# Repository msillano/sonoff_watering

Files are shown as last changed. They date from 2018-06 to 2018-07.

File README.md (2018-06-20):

# sonoff_watering

Tired of changing the terrace irrigation timer every 2 years, I decided to design a timer: obviously IoT and based on MQTT. 

The result is this complete DIY project of an irrigation timer, better than many commercial timers, designed and manufactured according to the state of the art. 

This timer contains a STA (WIFI client), an AP (not used), a MQTT client and a MQTT server (broker), provided with programmable logic (script): in practice a mini mosquitto + node-red on-board ! 

So in this project the operating logic is all internal: an external MQTT server 24/7 is not required (in fact I think a server 24/7 is too much to water a terrace!). The timer is totally autonomous, but at the same time always compatible with external standard MQTT clients and brokers. 

A probe monitors the state of the soil (dry/soaked, with adjustable threshold) and conditions the watering. 

Monitoring and configuration of the timer are performed with MQTT clients with dashboards, both on a PC and on a smartphone. Access is local via WIFI, but can be made Internet global using a free dynamic DNS service (example noip: https://www.noip.com/). 

While using updated and quality components, this timer is very cheap: total cost less than € 15 (US$ 18)!  All this is made possible by the happy union of two phenomenal products: 
1) Sonoff basic, economic WIFI card with power supply, microprocessor EPS8266 and relay
2) esp_MQTT, a firmware for EPS8266 created by Martin-ger, which transforms the Sonoff-basic into a tank. 

For the full story, see watering-sonoff-enXX.pdf (english version) or watering-sonoff-itXX.pdf (versione italiana).

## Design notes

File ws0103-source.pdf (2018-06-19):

% Watering-sonoff ver 1.3, GNU LGPL license, (C)2018 m.sillano % telnet: script http://192.168.43.242:85/www/sonoff/ws0103.eub

% you can change the topic and the ID in next line
config @6 /msillanohome/hidro/1

on init
do
% @8 is the run counter
% test for first run: $tmp = 0 also if @8 = '' setvar $tmp = (@8 * 1)
if $tmp = 0 then
% cool start, only for first run:
% @1: cycle timer count down (min: 0 off) setvar @1 = 0
% @2: cycle duration (min)
setvar @2 = 2
% @3: time T1
setvar @3 = "01:00"
% @4: time T2
setvar @4 = "02:00"
% @5: mode (0..4)
setvar @5 = 2
% @7: day counter (for mode 1) setvar @7 = 0
endif
% hot start
% increments run counter
setvar @8 = ($tmp + 1)
% sets topics
setvar $cmt = @6 | "/command"
setvar $set = @6 | "/set"
subscribe local $cmt
subscribe local $set
% set moisure status in var $ms gpio_pinmode 14 input
setvar $ms = gpio_in(14)
% publish status/moisure.
setvar $tmp = @6 | "/status/moisure"
publish local $tmp "{\"Time\":\"" | $timestamp | "\",\"moisure\":" | $ms | "}"
retained
% relay restore status, in var $rs
% restore from retained message...
setvar $tmp = @6 | "/status/watering"
setvar $rs = json_parse("watering",retained_topic($tmp)) if not($rs = 1) then
% default is 0
setvar $rs = 0
endif
% or from cycle timer count down if @1 > 0 then
setvar $rs = 1
% restart timer 1 (1 min)
settimer 1 60000
endif
% like a call: this publish status/watering and status/moisure publish local $cmt "go"
% sets alarms
setalarm 3 @3
setalarm 4 @4

on mqttconnect
do
% subscrive from new client all commands

subscribe remote $cmt
subscribe remote $set
% re-publish status to update new client publish local $set "{\"data\":\"send\"}" publish local $cmt "send"

on topic remote $set
do
% debug echo on console
println "on Remote Set " | $this_data
% re-publish local for execution publish local $set $this_data

on topic remote $cmt
do
% debug echo on console
println "on Remote Command " | $this_data
% re-publish local for execution
publish local $cmt $this_data

on topic local $set
do
% debug echo on console
println "on Local Set " | $this_data
% decodes the 'set' data, puts it in $tmp setvar $tmp = json_parse("data",$this_data)
if $tmp = "long" then
% sets cycle duration (min)
setvar @2 = json_parse("value",$this_data) | " "
endif
if $tmp = "when1" then
% sets time T1...
setvar @3 = json_parse("value",$this_data) % and update alarm 3
setalarm 3 @3
endif
if $tmp = "when2" then
% sets time T1...
setvar @4 = json_parse("value",$this_data) % and update alarm 4
setalarm 4 @4
endif
if $tmp = "mode" then
% sets mode (0..4)
setvar @5 = json_parse("value",$this_data) endif
if $tmp = "reset" then
% does reset
system reset
endif
if $tmp = "timezone" then
% sets timezone (see https://github.com/martin-ger/esp_mqtt/issues/36 )
system "set ntp_timezone " | json_parse("value",$this_data)
endif
% implicit 'send'
% in any case, after a 'set', publish status/config
setvar $tmp = @6 | "/status/config"
publish local $tmp "{\"run\":" | @8 | ",\"long\":" | @2 | ",\"tx\":[\"" | @3 |
"\",\"" | @4 | "\"],\"mode\":" | @5 | "}" retained

on topic local $cmt
do
% debug echo on console
println "on Local Command " | $this_data

% decodes the value
if $this_data = "on" then
% sets ON
setvar $rs = 1
endif
if $this_data = "off" then
% sets 0 cycle timer count down setvar @1 = 0
% sets OFF
setvar $rs = 0
endif
if $this_data = "toggle" then % sets 0 cycle timer count down setvar @1 = 0
% inverts relay status
setvar $rs = not($rs)
endif
% cycle starts only if moisure dry ($ms=1)
if (($this_data = "cycle")*($ms = 1)) > 0 then % sets ON
setvar $rs = 1
% initialize cycle timer count down
setvar @1 = (@2 + 1)
% start timer (60 sec)
settimer 1 60000
endif
setvar $tmp = @6 | "/status/watering"
if $this_data = "send" then
% only re-send status/*
publish local $tmp retained_topic($tmp)
setvar $tmp = @6 | "/status/moisure"
publish local $tmp retained_topic($tmp) else
% implicit 'go': set output and publish
if (($rs = 1)*(@5 = 4)) > 0 then
% mode 4, ON. Like $ms
gpio_out 12 $ms
gpio_out 13 not($ms)
else
% default
gpio_out 12 $rs
gpio_out 13 not ($rs)
endif
% publish the watering status
publish local $tmp "{\"Time\":\"" | $timestamp | "\",\"watering\":" | $rs |
"}" retained
endif

% Sonoff-basic button pressed:
on gpio_interrupt 0 pullup
do
% debug echo on console
println "New state GPIO 0: " | $this_gpio
if $this_gpio = 0 then
% toggle action
publish local $cmt "toggle"
endif

% status change of moisure probe on gpio_interrupt 14 nopullup
do
% debug echo on console
println "New state GPIO 14: " | $this_gpio
% real change?

if $ms = not($this_gpio) then
setvar $ms = $this_gpio
% publish the moisure status
setvar $tmp = @6 | "/status/moisure"
publish local $tmp "{\"Time\":\"" | $timestamp | "\",\"moisure\":" | $ms |
"}" retained
if (($rs = 1)*(@5 = 4)) > 0 then
% relay ON/OFF if mode 4 and $rs=1
gpio_out 12 $ms
gpio_out 13 not($ms)
endif
endif

% timer 1 min
on timer 1
do
% debug echo on console
println "on int timer1 " | @1
if @1 > 0 then
% down cycle timer count
setvar @1 = (@1 – 1)
% restart timer
settimer 1 60000
endif
if @1 = 1 then
% end count, sets OFF
publish local $cmt "off"
endif

% time T1 alarm
on alarm 3
do
% debug echo on console
println "on intT1"
setvar @7 = not(@7*1)
if ((@5 = 1)*(@7 = 1)) > 0 then % mode 1, if @7, starts cycle publish local $cmt "cycle" endif
if @5 > 1 then
if @5 = 4 then
% mode 4, sets ON
publish local $cmt "on"
else
% mode 2, 3: starts cycle
publish local $cmt "cycle" endif
endif

%time T2 alarm
on alarm 4
do
% debug echo on console
println "on intT2"
if @5 = 4 then
% mode 4: OFF
publish local $cmt "off"
endif
if @5 = 3 then
% mode 3: starts cycle
publish local $cmt "cycle" endif

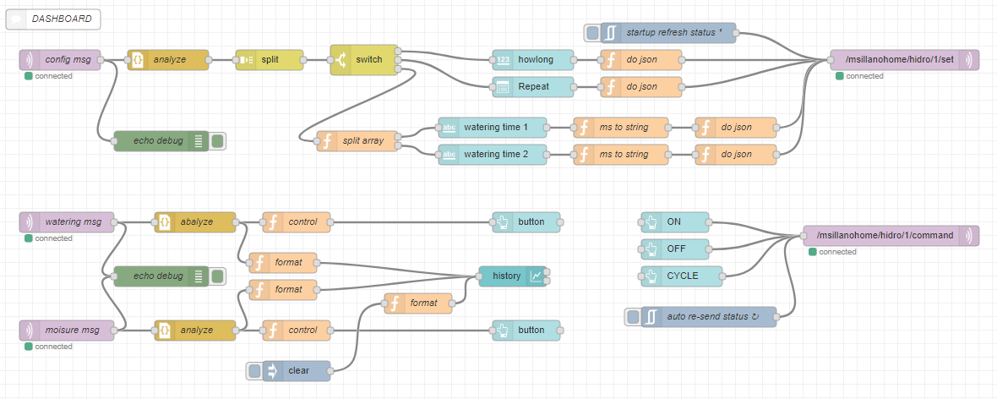
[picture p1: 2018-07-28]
images/2018-05-21.085833.shot.png

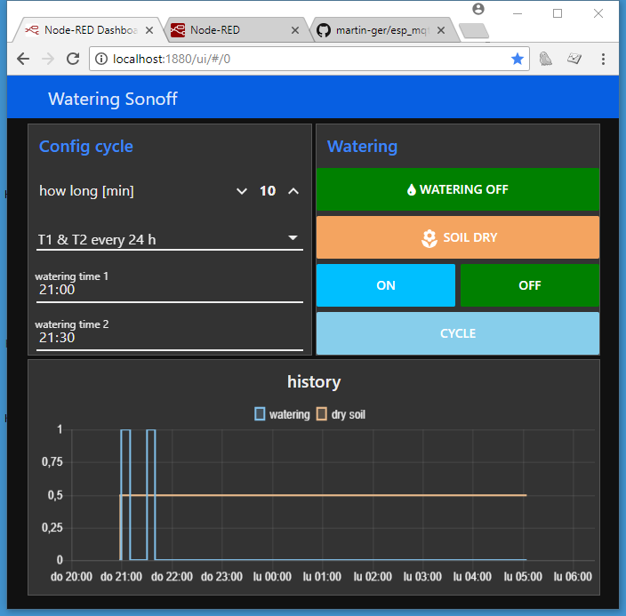
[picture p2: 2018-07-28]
images/2018-05-21.050436.shot.png

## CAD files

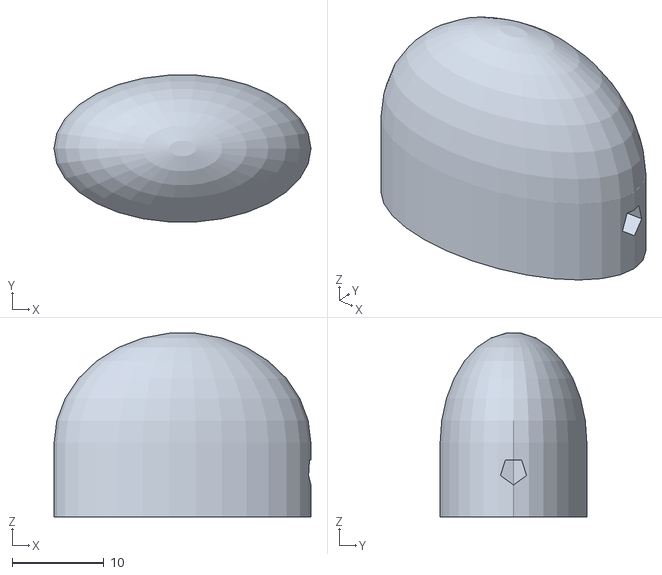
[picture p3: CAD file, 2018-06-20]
3d/sensor.stl
28.0 x 16.0 x 20.0

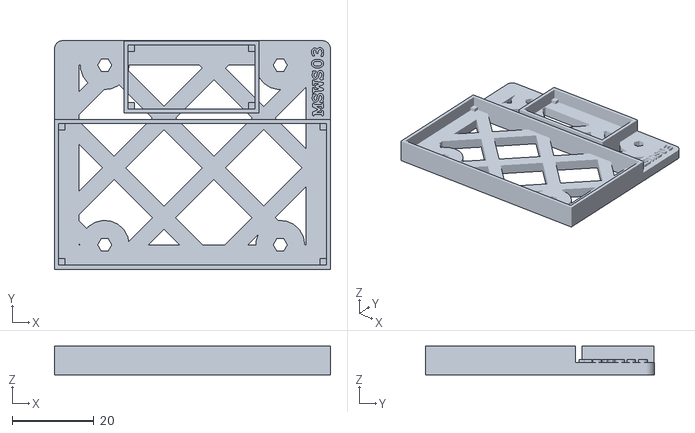
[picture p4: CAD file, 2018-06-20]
3d/e3DHW_base_lib.stl
67.6 x 56.0 x 7.00

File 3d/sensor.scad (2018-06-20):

 difference() {
   resize([28,16,20]) 
       union() {
           difference() {
                sphere(r = 12);
                sphere(r = 10);
                translate([-15, -15, -30]) {cube(size =[30,30,30]);};
           }
           translate([0, 0, -8+0.1])
                difference() {
                    cylinder(h= 8, r = 12);
                    cylinder(h= 8, r = 10);
           };
      }
      translate([10, 0, -3])rotate(a=[0,90,0])cylinder(h= 16, r = 1.5);   

    }

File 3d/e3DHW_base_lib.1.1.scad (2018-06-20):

/*
   e3DHW project © 2018 Marco Sillano  (marco.sillano@gmail.com)
   This library is free software: you can redistribute it and/or modify
   it under the terms of the GNU Lesser General Public License as published
   by the Free Software Foundation, either version 3 of the License, or
   (at your option) any later version.

   This project is distributed in the hope that it will be useful,
   but WITHOUT ANY WARRANTY; without even the implied warranty of
   MERCHANTABILITY or FITNESS FOR A PARTICULAR PURPOSE. See the
   GNU Lesser General Public License for more details.
   Designed with: http://www.openscad.org/
   Tested with: 3DRAG 1.2 https://www.futurashop.it/3drag-stampante-3d-versione-1.2-in-kit-7350-3dragk
*/
/*
 The e3DHW project is a set of libraries and things in OpenSCAD to make actual DIY electronics hardware in a simple and modular way (see e3DHW_HOWTO.pdf).

 This base library generates an hollow or solid slab of any shape, to be used as structural support for electronics modules and devices.
 An hollow base with a square grid pattern:
     - uses less material
     - allows air circulation
The base board can be used alone to place many small pcb in a container, or can be used with DIN rail clips (see e3DHW_base_lib.scad) or... as you like.
 Above the base can be placed several addons (see files e3DHW_addon_xxxxx.scad) as spacers, terminals etc.

MAIN MODULES
 polyBase:  makes a hollow base board of any shape, using 2 arrays for vertex and holes.
 
 rectangleBase: easy module for rectangular hollow boards with 4 mounting holes.
 
More public in this library:
Constants:
note: public capital constants are used as default values here and in other e3DHW libraries: you can redefine them in your file (global change) or you can use the method parameters (local change), as you need.
EXTRA = 0.1;  // quantum anti non-manifold error.
BOARDTHICKNESS = 3; // default base board thickness
BORDERTHICKNESS = 2; // default border thickness
DEFAULTFILL = 40;  // default hollow factor
note: The grid as a long rendering time. For fastest tests you can use fill=0 or 100.

Modules:
 getBorder: utility module widely used in other e3DHW libraries.

 see also:
 The file e3DHW_pcb_board_data.scad is a collection of commercial pcb geometries, to be used with polyBase().
 The file e3DHW_addon_base.scad is a collection of util things that you can place on base board (see exemples).
 
All e3DHW designs are experimental and may change.

The exemple STL file is from a real project: a timed watering system with local rain detection, controlled via MQTT (IoT).

ver. 0.1.1    18/03/2018 base version
*/

/*
Instructions
How to use "e3DHW_base_lib.scad" library:
  - put all libraries in same directory as your project.
  - In your OpenSCAD code add on top: "include <e3DHW_base_lib.scad>;" then you can use this public modules as you like.

 Tested using 3DRAG, PLA, layer 0.2, perimeter 4 layers, infill 40%-60%.
 For a professional result, choose a high temperature and approved Flame Retardant filament.
*/

include <MCAD/polyholes.scad>
// -------------- parameters  (change with care)

EXTRA = 0.1;  // quantum anti non-manifold error.
BOARDTHICKNESS = 3;
BORDERTHICKNESS = 2;
DEFAULTFILL = 40;

// locals, privates:
_gridSolid = 4;   // square grid solid width (mm)
_gridAngle = 45;
_slabborder = 6;   // board perimetral border (mm)
_slabcorner = 2;   // board round corners (radius, mm)

_slabHoleClearance = 6;   // solid border around mounting holes (radius, mm)

_printer_max_x = 200;  // limits of 3D printer
_printer_max_y = 200; 
//======================= EXPORT MAIN MODULES

// polyBase: makes a hollow base of any shape, using the arrays vertex and holes.
// parameters:
// vertex is an array of points: [[p1.x, p1.y],[p2.x,p2,y],...]
//     x range: mm [0.._printer_max_x], y range: mm [0.._printer_max_y]]
// holes is an array of mounting holes: [[h1.x,h1.y,h1.d],...]. Each hole will have around a solid circular border (_slabHoleClearance).
// fill: a value in percent: 0 (empty)... 100 (solid), usual range 20..50. (default DEFAULTFILL)
// thickness: board thickness. (default BOARDTHICKNESS)
// note: the square holes in hollow grid are calculated from fill and _gridSolid parameter: smaller _gridSolid value produces smaller holes.
module polyBase(vertex, holes, fill= DEFAULTFILL, thickness =BOARDTHICKNESS){
    intersection(){
      _do_baseh(vertex, holes, fill, thickness);
      translate([0,0,-EXTRA])_cut_base(vertex,thickness+2*EXTRA);
      }
}

//rectangleBase: easy module for rectangular hollow boards with 4 mounting holes. See images for parameters.
// holex: x holes distance 
// holey: y holes distance
// dxl, dxr: x border, left and right (board x size = holex+dxl+dxr)
// dyu, dyl: y border, up and low (board y size = holey+dyu+dyl)
// dhole: holes diameter
// fill: a value in percent: 0 (empty)... 100 (solid), usual range 20..50. (default DEFAULTFILL)
// thickness: board thickness. (default BOARDTHICKNESS)

module rectangleBase(holex, holey, dxl=10, dxr=10, dyu=10, dyl=10, dhole = 3, fill= DEFAULTFILL, thickness =BOARDTHICKNESS) { 
    rectPoints = [[0,0],[holex+dxl+dxr,0],[holex+dxl+dxr,holey+dyu+dyl],[0,holey+dyu+dyl]];
    rectHoles = [[dxl,dyl,dhole],[dxl,holey+dyl,dhole],[dxl+holex,dyl,dhole],[dxl+holex,holey+dyl,dhole]];
   polyBase(rectPoints, rectHoles, fill, thickness); 
   }

//getBorder: utility module, generates borders from vertex (rounds corners).
// vertex is an array of points: [[p1.x, p1.y],[p2.x,p2,y],...]
// height: border height (vertical)
// b: border thickness (default BORDERTHICKNESS)
module getBorder(vertex, height, b = BORDERTHICKNESS){
 difference(){
    _cut_base(vertex, height);
    translate([0,0,-EXTRA])linear_extrude(height = height+2*EXTRA, convexity = 20, twist = 0)  offset(delta=-b) polygon(vertex); 
        }
    }

// ===================== private local modules
module _do_grill(f,h){
    if (f > 98){
        cube([_printer_max_x+50,_printer_max_y+50,h],false);
    }  else {
        t = sqrt(100/(100-f-1));
        y = _gridSolid/(t-1);
       prtL = _printer_max_x> _printer_max_y ? _printer_max_x:_printer_max_y;
       translate([prtL/2,prtL/2,0])rotate([0,0,_gridAngle]) translate([-prtL*3/4,-prtL*3/4,0])union(){
          for (k = [0 : _gridSolid+y : prtL*3/2])  
             translate([k,0,0]) cube([_gridSolid,prtL*3/2,h],false); 
          for (j = [0 : _gridSolid+y : prtL*3/2])  
             translate([0,j,0]) cube([prtL*3/2,_gridSolid,h],false); 
       }
    }
 }
 
module _cut_base(vertex, hb){
    linear_extrude(height = hb, convexity = 20, twist = 0,$fn=64) offset(r=_slabcorner) offset(delta=-_slabcorner) polygon(vertex); 
}

module _do_baseh(vertex, holes, fill, s) {
difference(){
   union(){
      intersection(){
         _do_grill(fill, s);
         translate([0,0,-EXTRA])_cut_base(vertex,s+2*EXTRA);
         }
       getBorder(vertex, s, _slabborder);
       for (n =[0:1:len(holes)-1]) translate([holes[n].x,holes[n].y,0]) cylinder(r=_slabHoleClearance, h=s);
    }
   for (n =[0:1:len(holes)-1]) translate([holes[n].x,holes[n].y,-EXTRA]) polyhole(2*s,holes[n].z);
    }
}
/*
// =================== EXAMPLE
// base support for scheduled irrigation system with sonoff-basic + humidity meter (https://www.banggood.com/Soil-Hygrometer-Humidity-Detection-Module-Moisture-Sensor-For-Arduino-p-79227.html), to fit in Itead box
// see photos
include <e3DHW_addon_base.1.1.scad>        // the base board addons
include <e3DHW_pcb_board_data.1.1.scad>    // Sonoff pcb data

module watering_Sonoff03(){
   union() {
     rectangleBase(43,44,12.3,12.3,6,6); // base: size from Itead box
     //here you add and translate addons as reqired
     translate([0,0,0])add_polyBox(sonoffBasicVertex);
     translate([17,38.3,0])add_rectangleBox(30.50,15.08); // humidity meter pcb
     translate([66,38.3,0])add_text(txt="MSWS03", size=3, rot=[0,0,90]);
     }
  }
// top level geometry:
watering_Sonoff03();
*/

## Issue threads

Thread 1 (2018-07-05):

Like and Hint

martin-ger, 2018-07-05:
Marco,

really like the project, the complete approach, the exhaustive description, and of cause the extensive use of the esp_mqtt.

Perhaps one hint. I recently had a student project with this kind of humidity sensors: they suffer from heavy corrosion and tend to fail after some weeks. There are better capacitive sensors with glass housing available - of course these are more expensive and not so easy to read...

msillano, 2018-07-27:
Thanks Martin
This is a low budget project... i seen also resistive sensors covered with gypsum....
I make some changes: added hysteresis to comparator, and polling (one min) in place of interrupt in mode 4.... too many switchings close to the threshold :(

Next: a simple timer for orchis and hidroponics (ebb and flow)

These projects are spin-off of the main project: a professional control system for hydroponics....

esp_mqtt wonderful :)

msillano, 2018-08-02:
The new version (01.03.3) uses polling (in place of interrupt) for the  humidity sensors.
The probe-comparator circut is powered via GPIO-1, only 100 ms every minute.
That must reduce radically  the bad electrolytic effects on probe.
Thanks for the hint,
Best regards.

Closed 2018-08-02.

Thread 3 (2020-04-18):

Gpio1 to power the sensor-fail to boot

matejb123, 2020-04-18:
Hi,
Thanks for the wonderful project.
I have one problem though - if using gpio1 to power the sensor, the device would work if connecting the sensor after booting but would fail to boot with sensor attached.
I suspect the capacitor on the vcc of the comparator is pulling gpio1 down. Have you done anything with it? Did you not have problems with it?
Thanks and best regards,
Matej
